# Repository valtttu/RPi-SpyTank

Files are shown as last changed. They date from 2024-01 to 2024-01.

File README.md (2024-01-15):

# RC-SpyTank project

> Valtteri Turkki

This repo contains documentation for Raspberry Pi SpyTank project. The idea was to make a fairly low-cost RC tracked vechile. The end result (in the current state) is shown in the below photo:

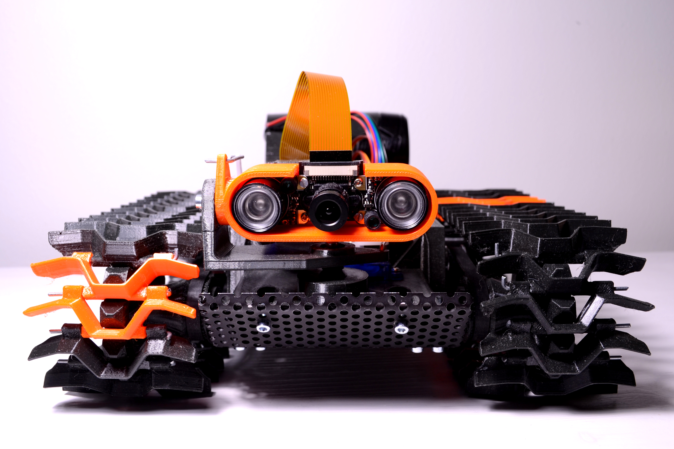
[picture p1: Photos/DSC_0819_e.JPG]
SpyTank


## Initial idea

Inspired by _RCTESTFLIGHT_ YouTube channels "_Tracked vehicles_" [playlist](https://youtube.com/playlist?list=PLXvxJNOIXBsN97d3_b5AXquRSAQOs3tVV&si=yVQvDruLYLw2IaSi), the idea was to build a RC-track vehicle for mainly indoor use. The key parameters are:

- Footprint of rougly one A4 sheet
- 3D printed tracks that can handle various types of terrain
- Controlling via Raspberry Pi
- Possibility to stream onboard night vision camera footage to phone
- Controlling with a bluetooth gamepad 
- Silent enough operation -> allows for spying in the dark

The 3D models for the tracks and pulleys that were used as the basis of the design are from _RCTESTFLIGHT_ Thingiverse page "_Snow Tank_" [https://www.thingiverse.com/thing:4308626](https://www.thingiverse.com/thing:4308626). Below photo shows that Snow Tank.

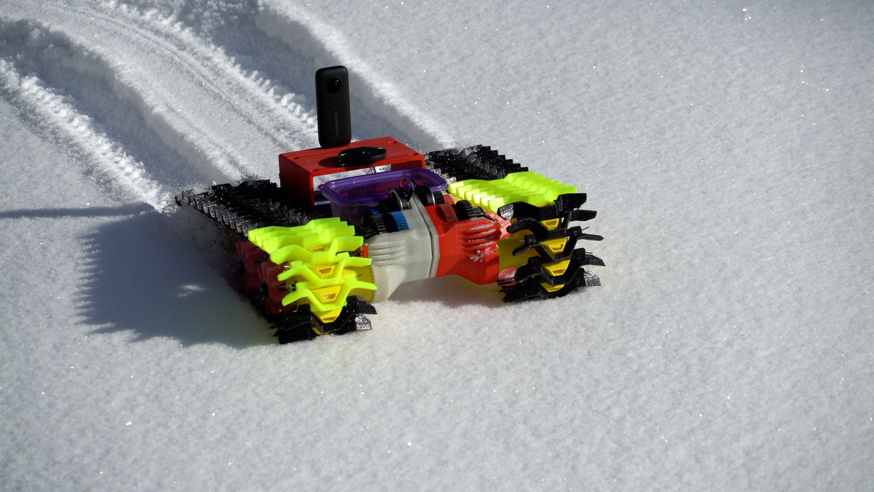
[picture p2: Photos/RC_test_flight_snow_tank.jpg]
Snow Tank by RCTESTFLIGHT


## Components

### Component choices explained

The main board was chosen to be Raspberry Pi zero 2 W as it has small footprint and power consumption, but it still allows you to plug-in the camera directly. The camera was chosen to be the ZeroCam night vision model as it plugs directly into the Pi Zero and allows decent image quality.

The motors were chosen to be NEMA 17 steppers due to the fact that they offer good torque and can be very silent with the Trinamic TMC2209 drivers. Also, as the tank was meant for silent operation and spying, the low top speed wasn't an issue. Furthermore, the NEMA 17 + TMC2209 combo costs as much as one good BLDC motor and you'd still need second motor and the controller...

The drilling machine battery was chosen as power supply as it's quite cheap and has a sturdy casing. If you have a 3S LiPo battery laying around, that's also a good option. The power conversion from 12v to 5v was made with a 'ghetto' solution: Buy a car USB adapter, tear it down and remove the connectors and there you have a step-down converter with 4 euros (compared to the fact that some step-down modules that can do >2A cost more than 20 euros).

### Component list

- Raspberry Pi Zero 2 W, link: [https://www.partco.fi/en/raspberry-pi/raspberry-pi-zero/23529-rpi-zero-2w.html](https://www.partco.fi/en/raspberry-pi/raspberry-pi-zero/23529-rpi-zero-2w.html)
- Night vision camera link: [https://raspberrypi.dk/en/product/zerocam-nightvision/](https://raspberrypi.dk/en/product/zerocam-nightvision/)
- Wireless retro gamepad controller 8BitDo, link: [Verkkokauppa.com](https://www.verkkokauppa.com/fi/product/625627/8BitDo-SN30-Pro-G-Classic-peliohjain-Switch-PC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)
- 2x NEMA 17 Stepper motor, link: [https://kauppa.sintosen.com/product/1266/nema-17-stepperi-moottori-18-astetta](https://kauppa.sintosen.com/product/1266/nema-17-stepperi-moottori-18-astetta)
- 2x TMC2209 v2.0 Stepper driver, link: [https://kauppa.sintosen.com/product/676/tmc2209-v20-stepperi-ohjain](https://kauppa.sintosen.com/product/676/tmc2209-v20-stepperi-ohjain) 
- 2x Miniature servo motor for camera tilting and panning (Tower pro 9g), link: [https://www.partco.fi/en/electromechanics/motors/servo-motors/20291-servo-sg90.html](https://www.partco.fi/en/electromechanics/motors/servo-motors/20291-servo-sg90.html)
- 2x OD: 13 mm, ID: 6 mm, width: 6 mm bearings for camera axes (recycled from bicycle pedals), link: [https://www.ebay.co.uk/itm/266305894814](https://www.ebay.co.uk/itm/266305894814)
- 2x Timing belt 160 mm, link: [https://kauppa.sintosen.com/product/899/hammashihna-gt2-6mm-160mm-lenkki](https://kauppa.sintosen.com/product/899/hammashihna-gt2-6mm-160mm-lenkki)
- 2x Pulley, link: [https://kauppa.sintosen.com/product/582/ajoituspyora-gt2-20-hammasta-6mm-hihnalle](https://kauppa.sintosen.com/product/582/ajoituspyora-gt2-20-hammasta-6mm-hihnalle)
- Drilling machince battery Tamforce+ 12v 2Ah, link: [https://www.puuilo.fi/tamforce-akku-12v-2ah](https://www.puuilo.fi/tamforce-akku-12v-2ah)
- 12v to 5v step-down converter for Pi and servos, link: [https://www.puuilo.fi/axxel-usb-autolaturi-12v-kahdella-portilla](https://www.puuilo.fi/axxel-usb-autolaturi-12v-kahdella-portilla)
- 8x 6mm bearings for the wheels, link: [https://hobbyfactory.fi/p41450/avid-6x12x4-revolution-1kpl](https://hobbyfactory.fi/p41450/avid-6x12x4-revolution-1kpl)
- 2x springs for track tensioning, link: [https://hobbyfactory.fi/p41913/team-associated-91834-front-shock-springs-yellow-4-30-lb-in-l44mm](https://hobbyfactory.fi/p41913/team-associated-91834-front-shock-springs-yellow-4-30-lb-in-l44mm)
- 2x M5 bolt with 75 mm length for the track tensoner shaft
- 2x 6 mm rod, length 108 mm for the electronics rail
- 78 mm x 66 mm PCB for soldering the electronics
- M6 threaded rod for axles, link: [https://www.puuilo.fi/kierretanko-rst-a2-1m-m6](https://www.puuilo.fi/kierretanko-rst-a2-1m-m6)
- 1 mm sheet metal with 3 mm holes for the base plate
- approx. 50x M3 nuts and bolts (from 10 mm to 20 mm in length)

## Mechanical solutions

Here are explained some of the key mechanical features of the SpyTank:

### 1) Component placing



The use of perforated steel sheet with 3 mm holes as base plate allows to mount things easily and flexibly. All of the bolts to the bottom are M3 and the 3D models have slotted holes for the bolts, so that the exact position of the parts can be adjusted. The distribution of components is made so that the center of mass of the tank is quite well in the center and thus the tracks should have the lowest possible pressure.

### 2) Camera pan and tilt system

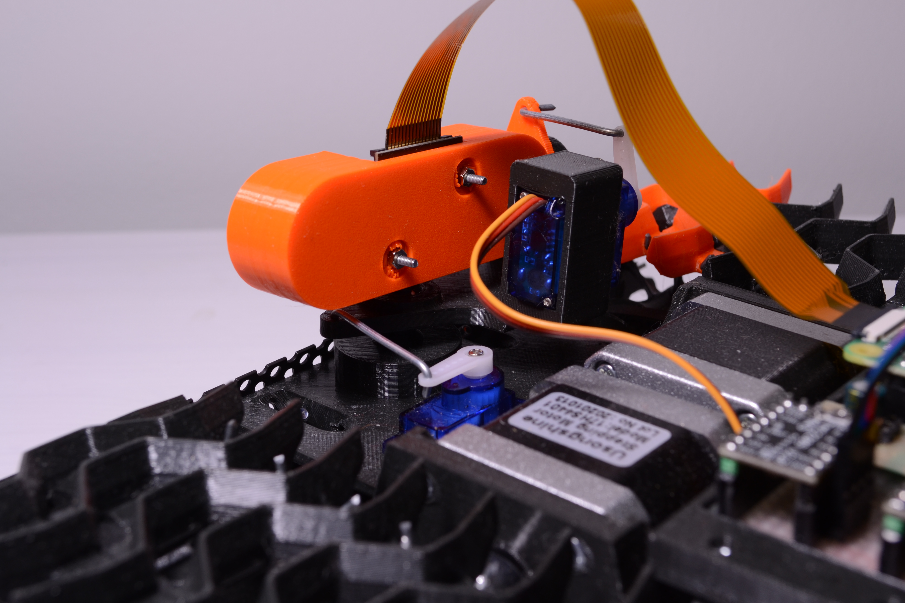
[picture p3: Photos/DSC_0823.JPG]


The pan & tilt functionality for the camera is done with 2 miniature servos and liknages made from the same steel wire as the track pins. The axes have bearings to enable smooth rotation. The holes in the servo arms had to be enlargened for the steel wire.

### 3) Front axis and belt tensioning



As the tank has tracks and belt drive, it means that the wheelbase and drive axle to motor shaft distances have to be modifiable. This is done so that motors are fixed on their place, but the front axle has slots in the track direction and thus the belt tension is adjusted by moving the front axle forward or backward. The gear ration is 2:1 which gives the tank already enough torque to climb a hill so steep that it will land on its roof.

### 4) Track tensioning and electronics mounting



In order to allow the track to adapt to the terrain, the rear axle is spring loaded with the tensioning system in the photo above. The axle goes through a holder that has M5 nut intergrated to it. The holder is then installed to a slider mount that also has the RC vehicle spring to provide the tension. To keep things moving linearly, a M5 bolt (75 mm) with the head cut away and a notch made for tightening is inserted to the center.

The electronics PCB and the battery are mounted on two rails. This allows easy attachement of them and also leaves room for future modifiability, in case the electronics gets updated.

## Programming and circuits

### The basic idea of interfaces

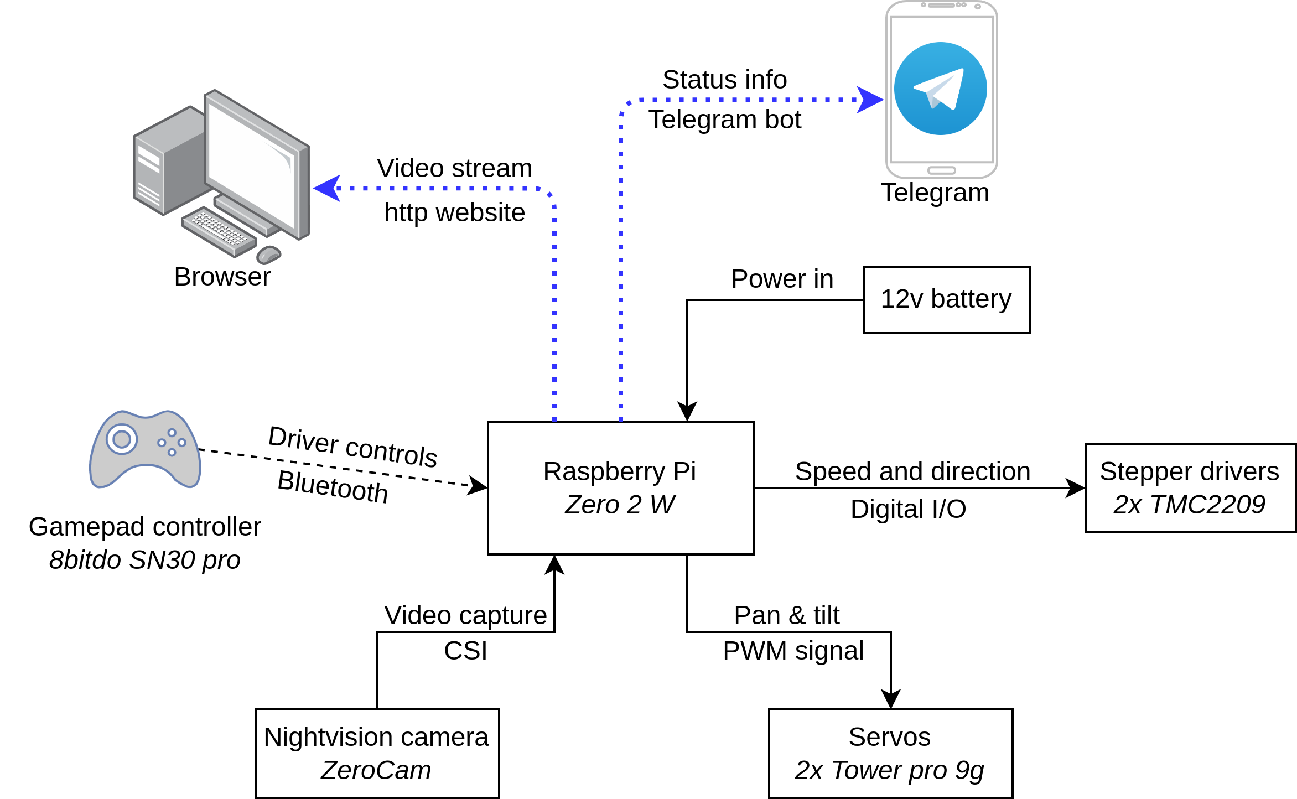
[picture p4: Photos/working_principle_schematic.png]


The 'mechatronic design schematic' of the SpyTank is shown in the above figure. 

### Wiring schematic

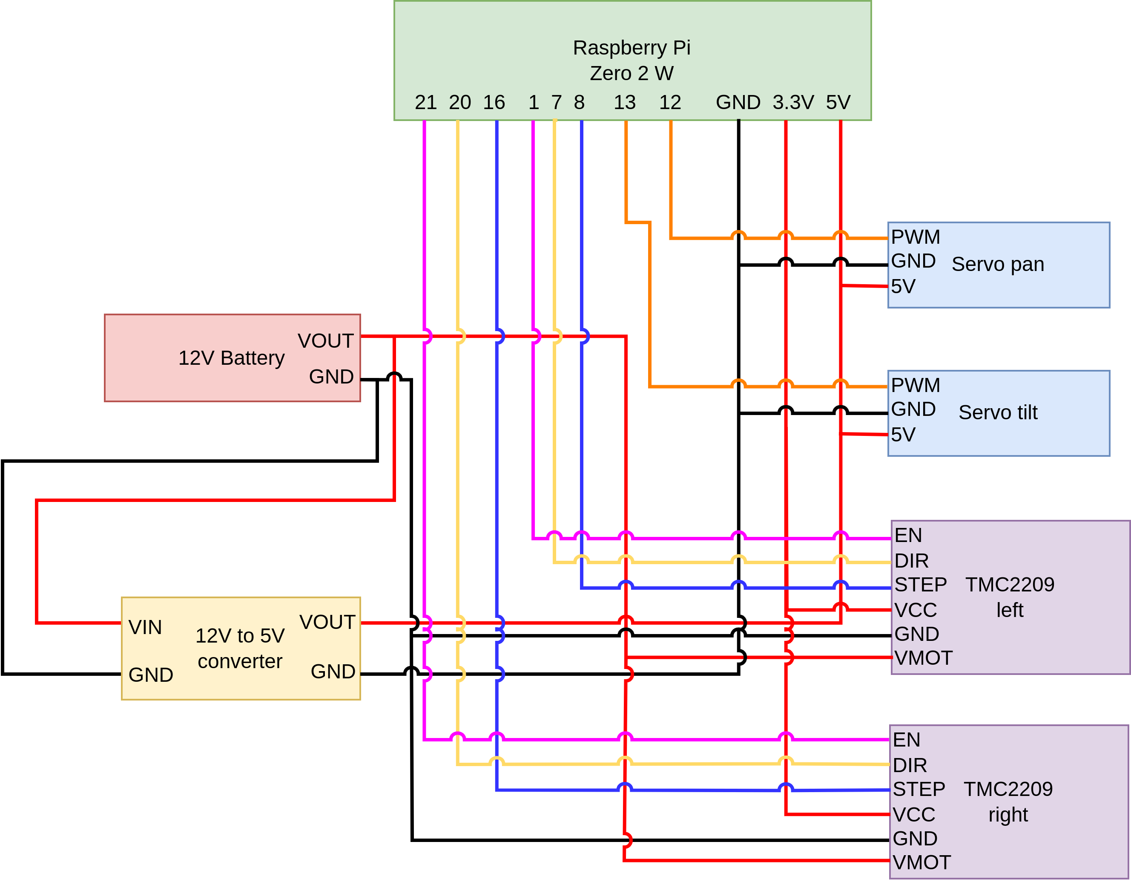
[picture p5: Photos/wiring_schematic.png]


The circuit plan pf the tank is shown above.

### Programming part

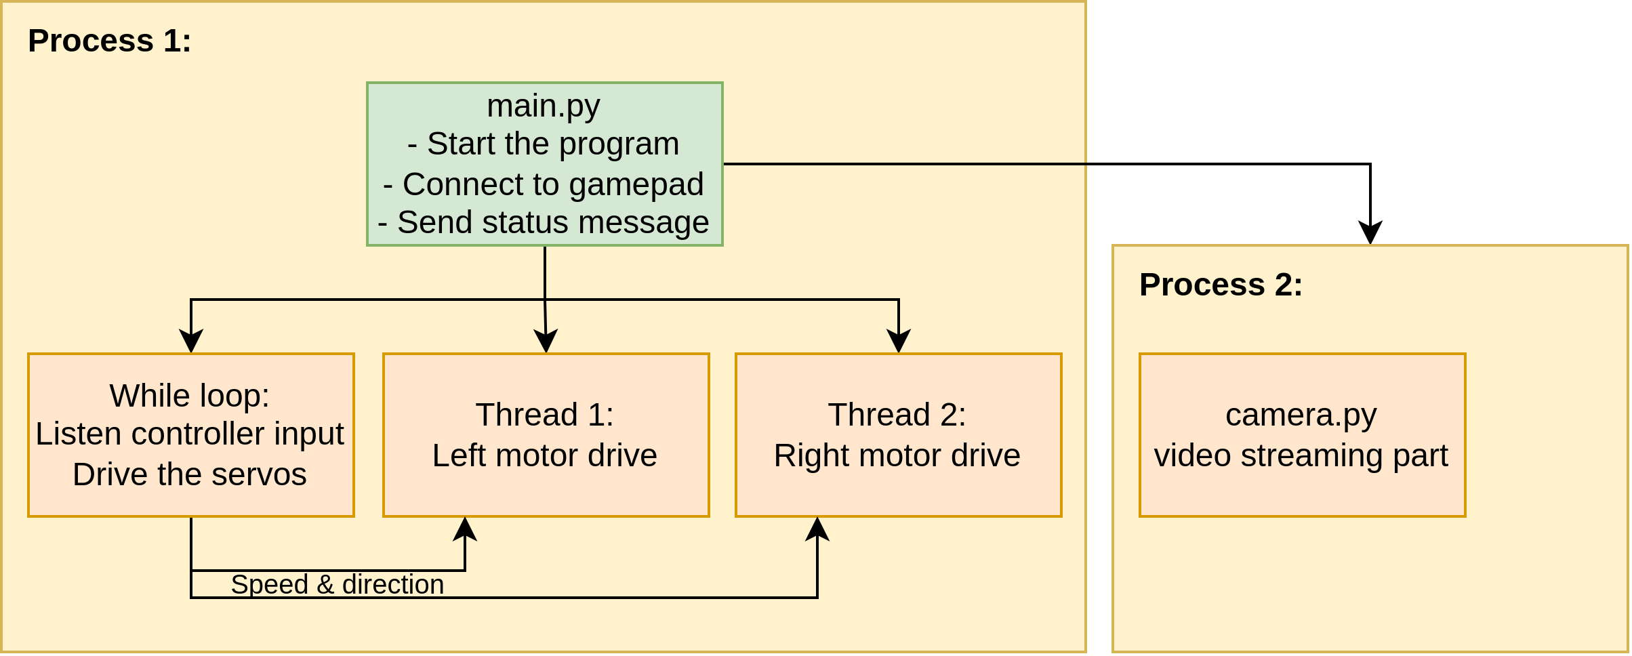
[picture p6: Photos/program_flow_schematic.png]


The diagram above explains the program logic of the SpyTank. There are 3 classes: `camera`, `motors` (in `stepper.py`) and `controller`. 

The camera class controls the servos of the camera stage and starts the stream. The stream works independently in its own process and is in the `server.py` script. The script is direcly the one from [github.com/waveform80/pistreaming/](https://github.com/waveform80/pistreaming/) with slight modifications to the paths, so that the script can be run from any directory. 

The motors class takes care of converting the input from the controller analog axis [-1, 1] to direction and step delay for right and left motor. Thus, the control is tank-like, ie. you use left analog stick to control left track and the right one for right track. The conversion for the delay is done linearly and there'a a cut-off so that input smaller than it maps to zero velocity $\rightarrow$ motors off.

The controller class takes care of mapping the buttons and axes of the gamepad controller to input. As `pyglet` didn't seem to work with the SN30 Pro controller in wireless more, the controller mapping is done with `evdev`. The implementation is such that adding new buttons should be rather straight forward (the mappings are told in `main.py`). To find more info how to use `evdev` and where the numbers come from, see [python-evdev.readthedocs.io/en/latest/](https://python-evdev.readthedocs.io/en/latest/).

The script `utils.py` contains some accessory functions that make the `main.py` cleaner to read. The Telegram bot messaging is made so that the bot credentials are stored in file `secrets.dat` in format `secret-name;secret-value` and read from there using function `read_credentials()`. Then the code finds the IP local address of the PI and parses a message that contains the IP and the stream link. The message is sent using the bot API as follows
```
url = f"https://api.telegram.org/bot{data['TOKEN']}/sendMessage?chat_id={data['ID']}&text={message}"
    requests.get(url).json()
```
where `TOKEN` is the bot token and `ID` is your Telegram ID (can be found by googling _"How to find my Telegram ID"_ and asking it from a bot).

Finally, to make the `main.py` run on boot up, the `rc.local` file of the Pi has to be modified accordingly: Add lines

```
sleep 15
sudo python3 /home/user-name/SpyTank/Code/main.py &
```
above the `exit 0`. Modify the path to match your code location and note the `&` as otherwise the code will stop the boot (`rc.local` will never exit). This will give the PI time to find network connection etc. After this, the `controller.connect()` method has a default timeout of 40 seconds. If the connection to that gamepad controller is not estabilised in this time, the code will exit.

## Additional instructions

### Baseplate cutting and bending

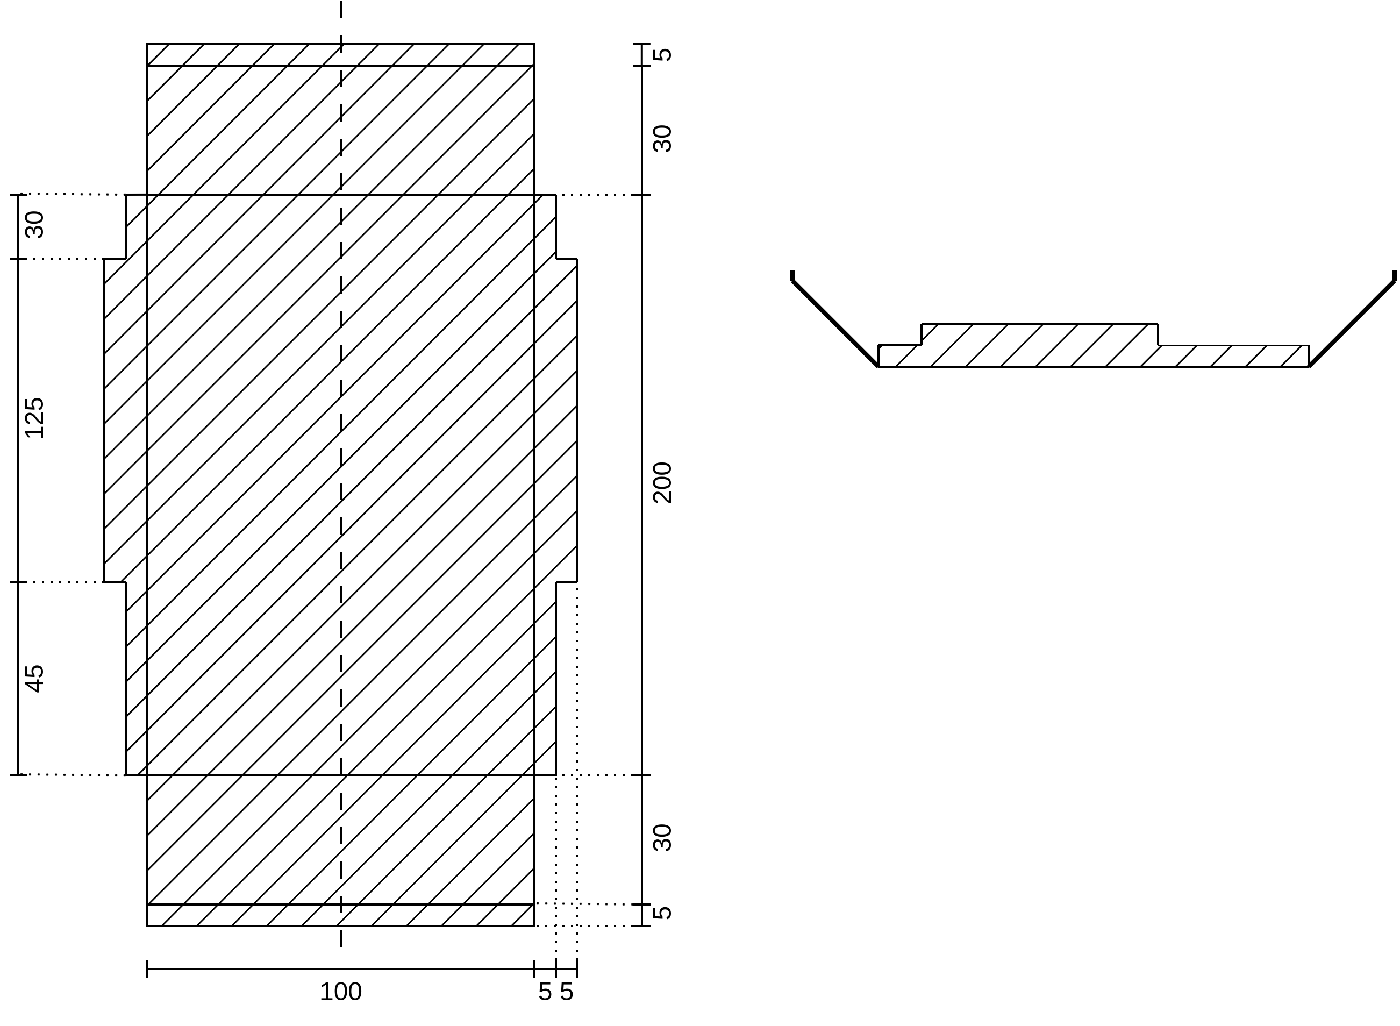
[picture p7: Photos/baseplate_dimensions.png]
Baseplate dimensions


Above is shown the baseplate dimensions. The plate is bent so that the ends are at 45 degree angle with respect to the bottom and the final parts are vertical. The sides are at 90 degree angle w.r.t. the bottom part.

### 3D printing specs

| **Model name** | **Orientation** | **Supports** | **Print in places**|
|---|---|---|---|
| `camera_base.stl` | As installed (pan axis along z-axis) | From the build plate | Insert 1x M3 nut | 
| `camera_holder.stl` | Backside (with the 2 holes) facing down | From the build plate | Insert 1x M3 nut | 
| `camera_pan_stage.stl` | As installed (pan axis along z-axis) | From the build plate | None | 
| `front_axle_holder.stl` | Axle hole aligned with z-axis | None | None |
| `front_axle_spacer.stl` | Hole aligned with z-axis | None | None |
| `front_pulley.stl` | The outside face of the pulley to build plate | None | None |
| `nema17_mount.stl` | Largest flat face to build plate | None | None |
| `rear_axle_holder.stl` | Axle hole aligned with horizontally | None | Insert 1x M5 nut |
| `rear_axle_holder_slider.stl` | So that the slotted hole on on the top is horizontally | None | None |
| `rear_axle_spacer.stl` | Axle hole aligned with z-axis | None | None |
| `rear_pulley.stl` | Same as `front_pulley.stl`| None | None |
| `track_link.stl` | So that the track pin holes are horizontally | None | None |
| `drill_battery_holder.stl` | The flat face with 2 holes facing down | Use enforcers for the rail mounts | None |
| `pcb_carrier.stl` | Top part (largest flat face) facing down | None | Insert the main PCB and 6x M3 nuts for enclosure attachment |
| `rail_holder_back.stl` | Rail hole axis aligned with the z-axis, holes opening upwards | None | None |
| `rail_holder_front.stl` | Axle hole aligned with z-axis, holes opening upwards | None | None |
| `rpi_pcb_spacer.stl` | Axle aligned with z-axis| None | None |
| `stepper_wire_connector.stl` | PCB and slotted holes vertically | None | Insert a small PCB |

All parts were printed with Prusa Mini using 0.4 mm nozzle and PETG filament. The default layer height was 0.25 mm (draft quality) and variable layer height was used for parts with holes that have to be precise and have axis perpendicular to z-axis while printing. For high mechanical stress parts (axle holders and pulleys), the number of perimeters was increased to 3 from the default 2.

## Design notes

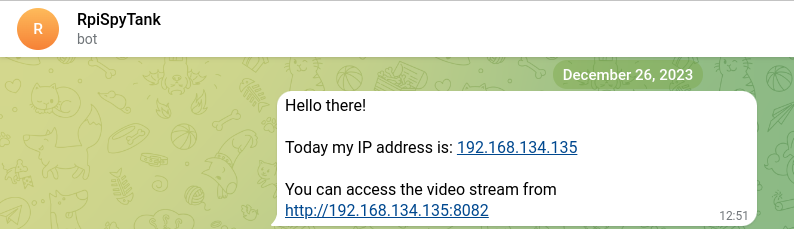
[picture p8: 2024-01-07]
Photos/telegram_bot_message.png

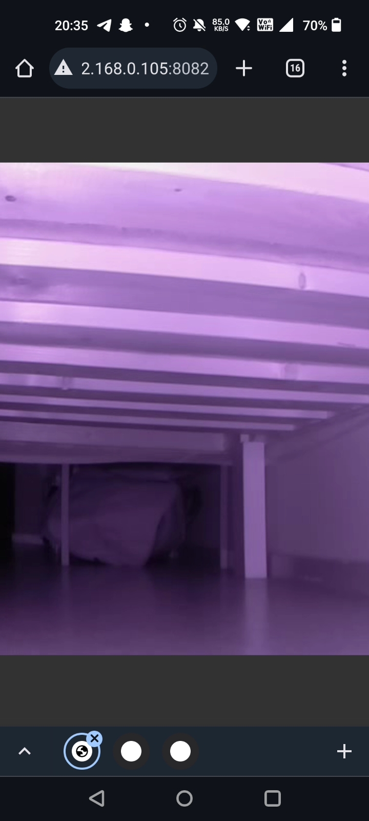
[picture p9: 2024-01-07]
Photos/nightvision_stream.jpg

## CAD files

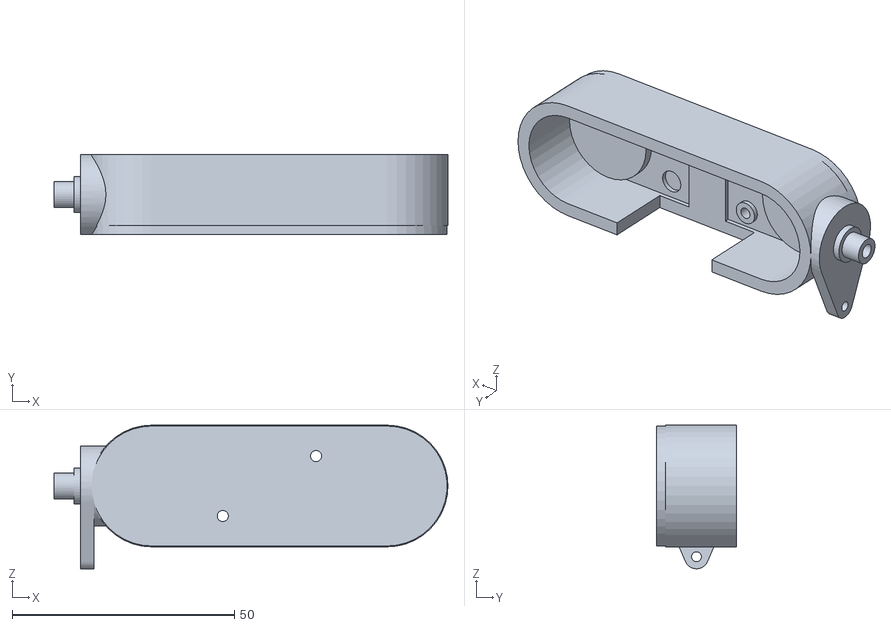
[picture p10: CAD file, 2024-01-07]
Models/Camera/camera_holder.STL
88.7 x 18.0 x 32.3

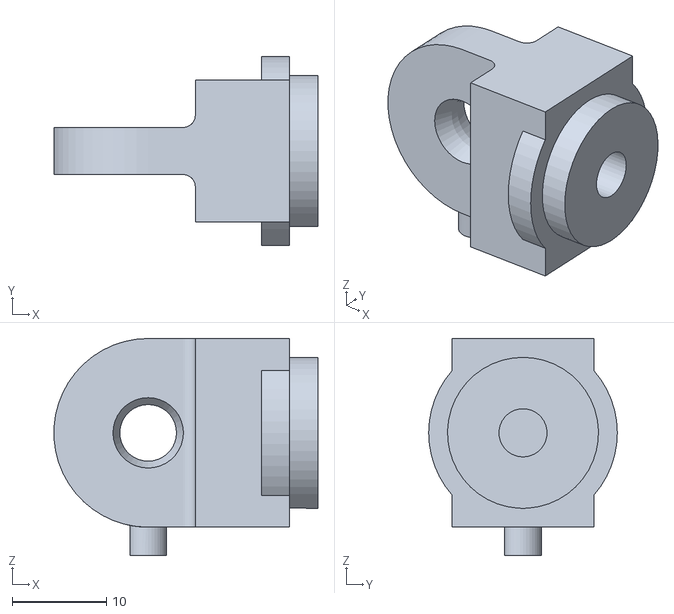
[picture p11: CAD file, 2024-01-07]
Models/Drivetrain/rear_axle_holder.STL
28.0 x 20.0 x 23.0

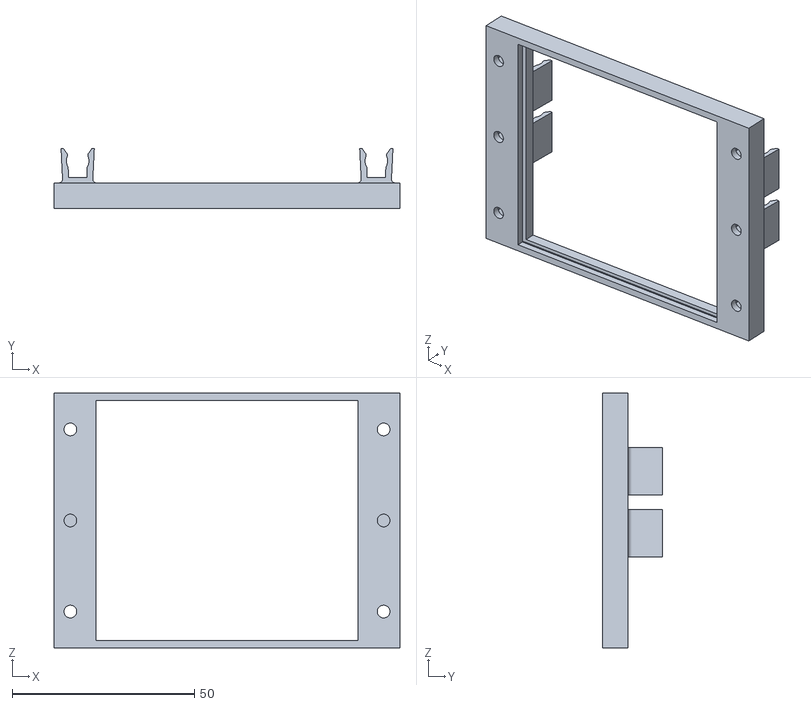
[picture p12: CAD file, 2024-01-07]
Models/Electronics/pcb_carrier.STL
95.0 x 16.4 x 70.0

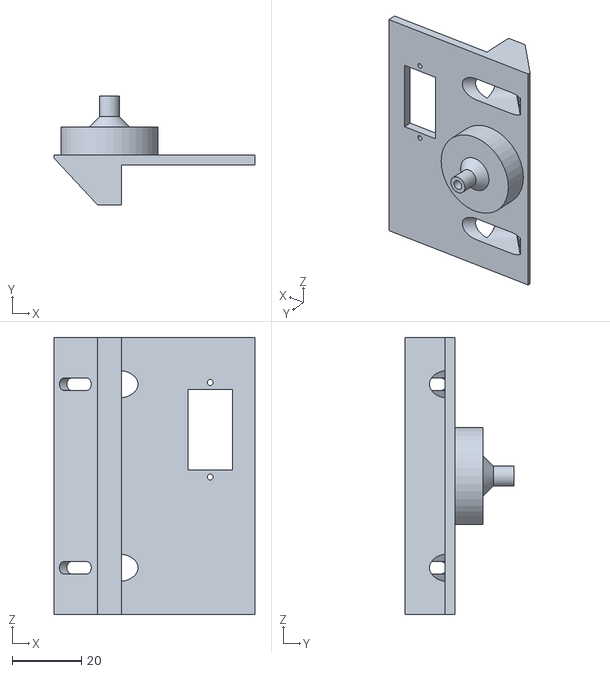
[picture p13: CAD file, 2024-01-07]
Models/Camera/camera_base.STL
58.0 x 31.5 x 80.0

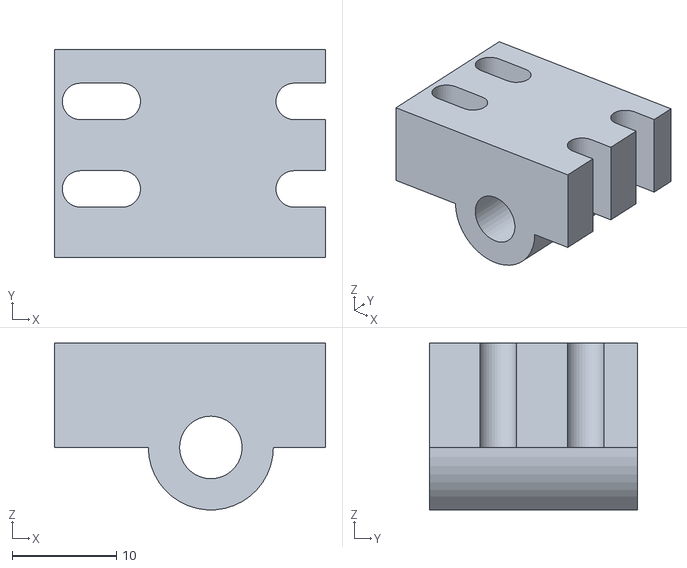
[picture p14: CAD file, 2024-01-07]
Models/Drivetrain/front_axle_holder.STL
26.0 x 20.0 x 16.0

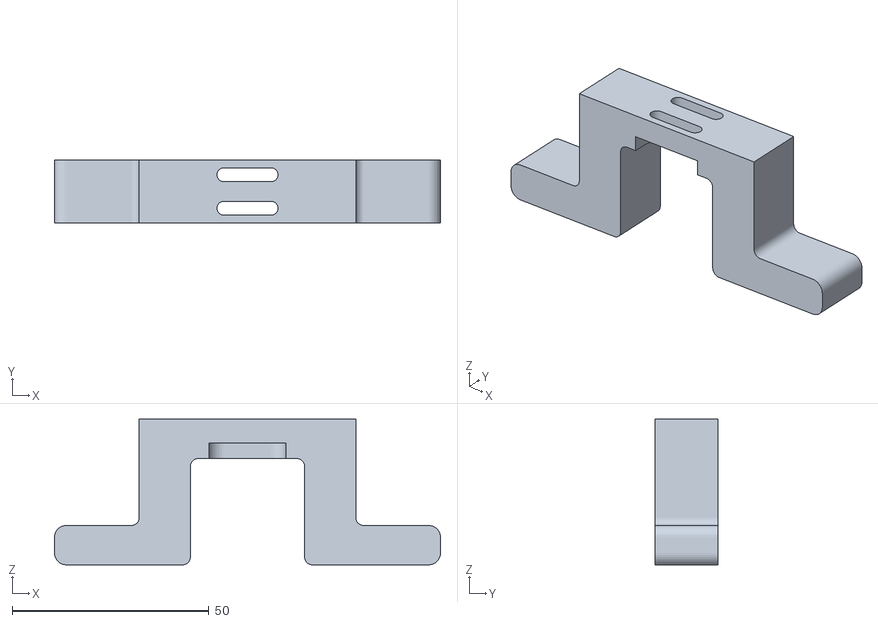
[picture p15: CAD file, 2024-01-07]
Models/Electronics/rail_holder_front.STL
98.0 x 16.0 x 37.0

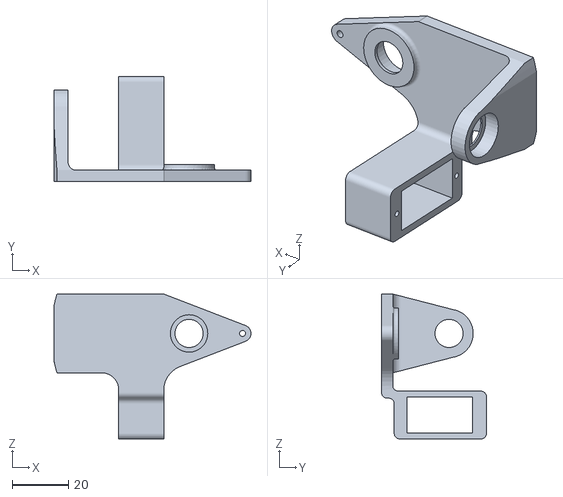
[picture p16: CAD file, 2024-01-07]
Models/Camera/camera_pan_stage.STL
70.0 x 37.3 x 51.5

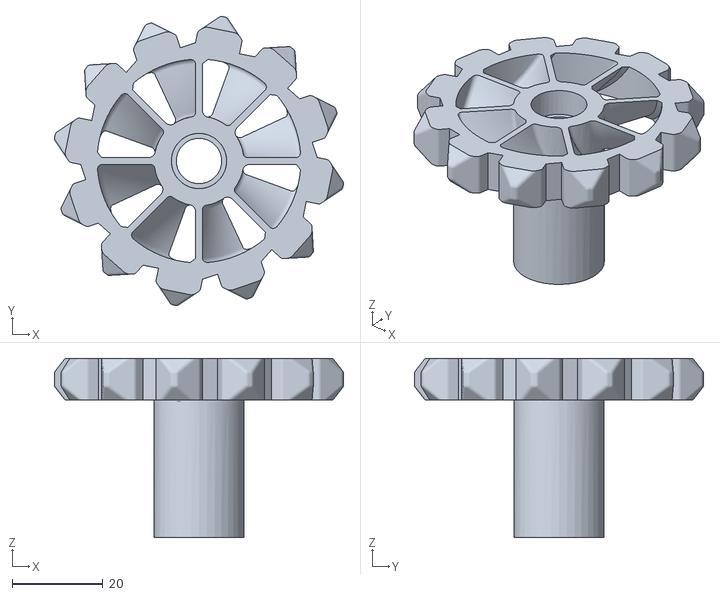
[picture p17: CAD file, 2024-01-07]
Models/Drivetrain/rear_pulley.STL
63.8 x 63.8 x 39.6

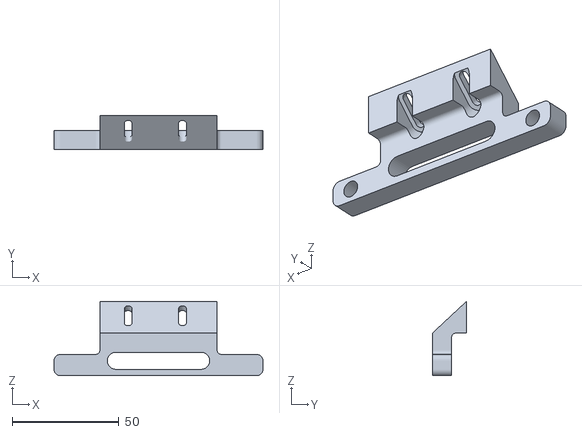
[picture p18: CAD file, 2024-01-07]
Models/Electronics/rail_holder_back.STL
98.0 x 16.0 x 34.9

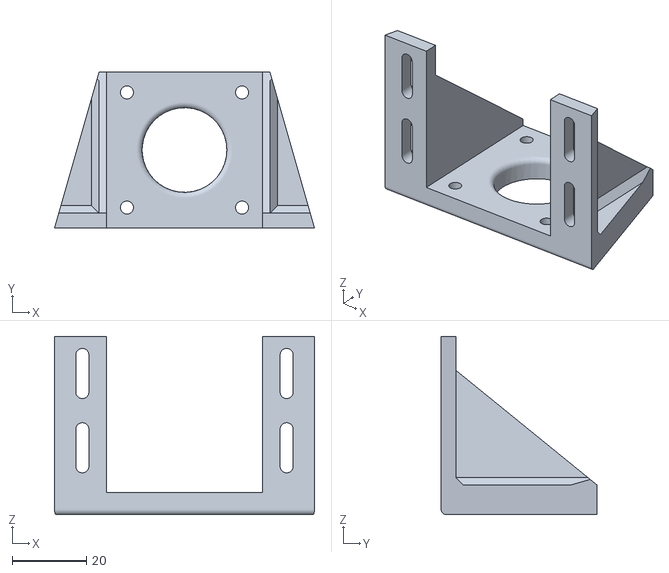
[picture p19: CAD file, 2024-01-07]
Models/Drivetrain/nema17_mount.STL
70.0 x 42.0 x 48.0

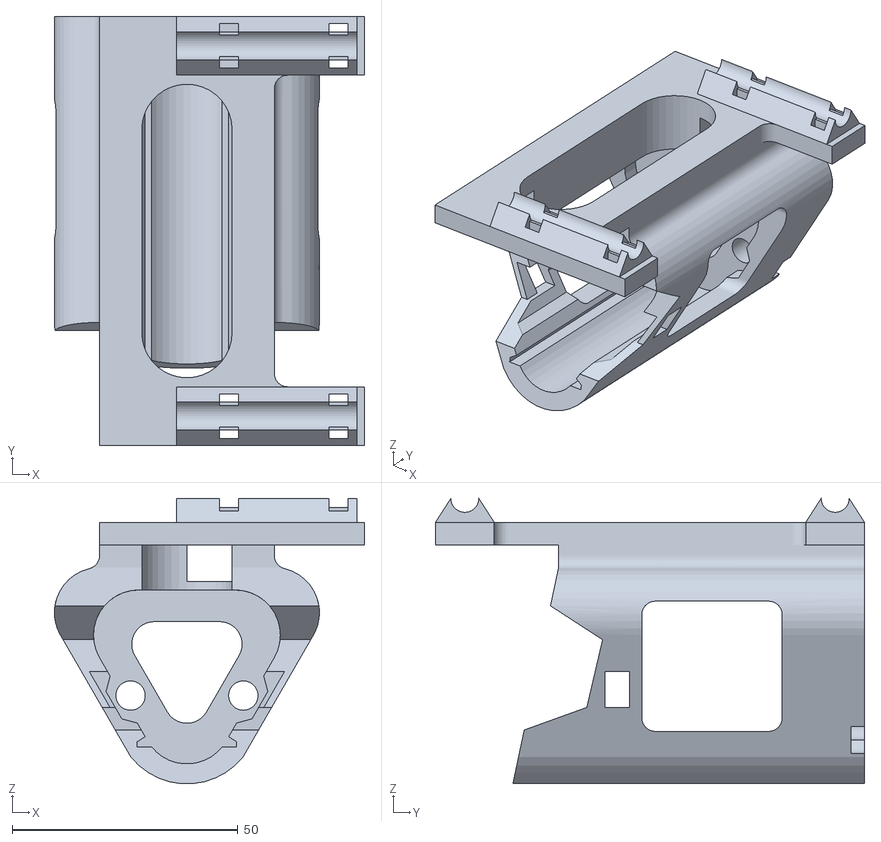
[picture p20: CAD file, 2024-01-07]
Models/Electronics/drill_battery_holder.STL
68.7 x 95.0 x 63.2

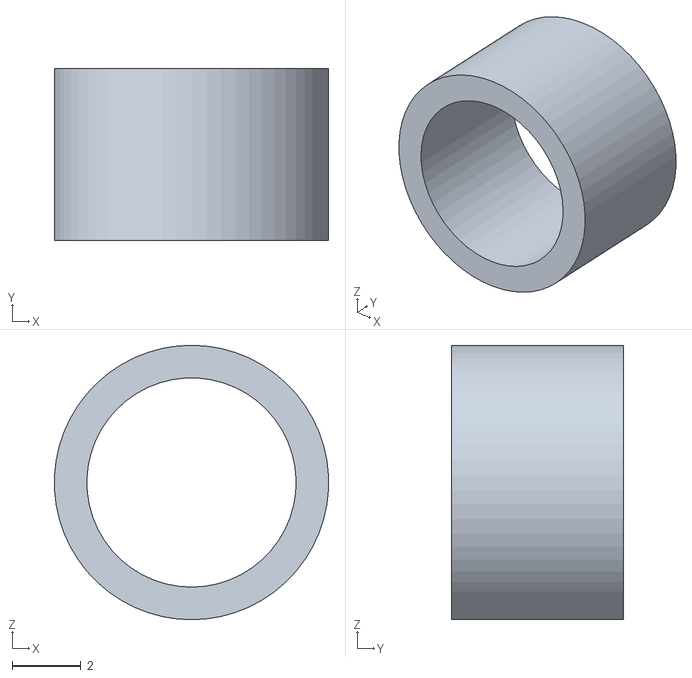
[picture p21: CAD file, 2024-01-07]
Models/Drivetrain/front_axle_spacer.STL
7.99 x 5.00 x 8.00

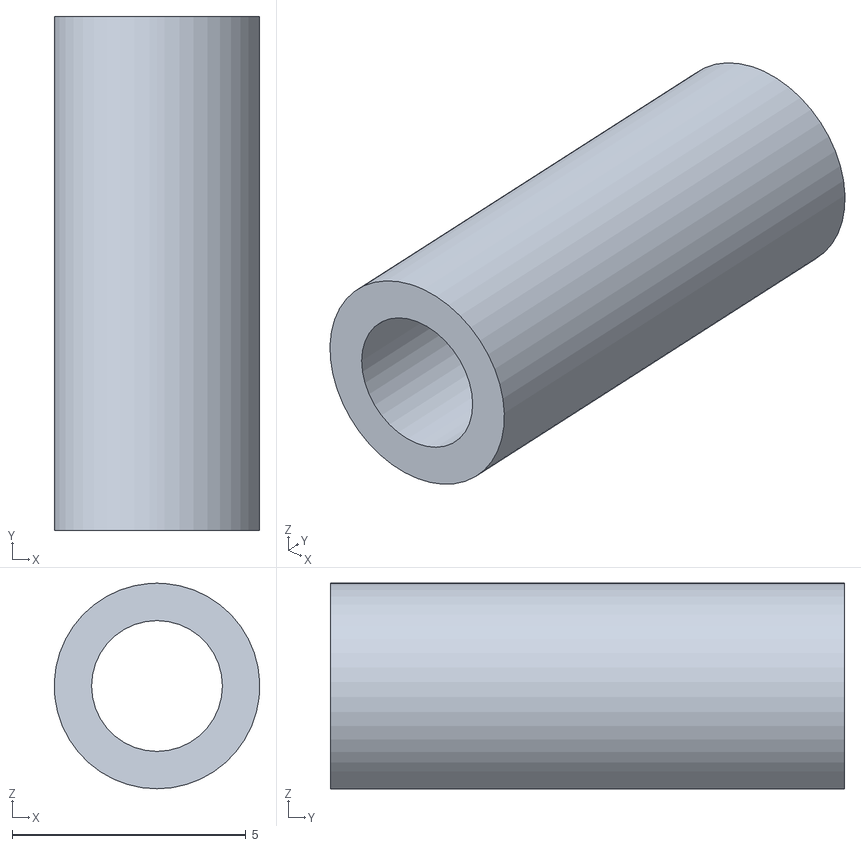
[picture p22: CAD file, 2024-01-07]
Models/Electronics/rpi_pcb_spacer.STL
4.40 x 11.0 x 4.40

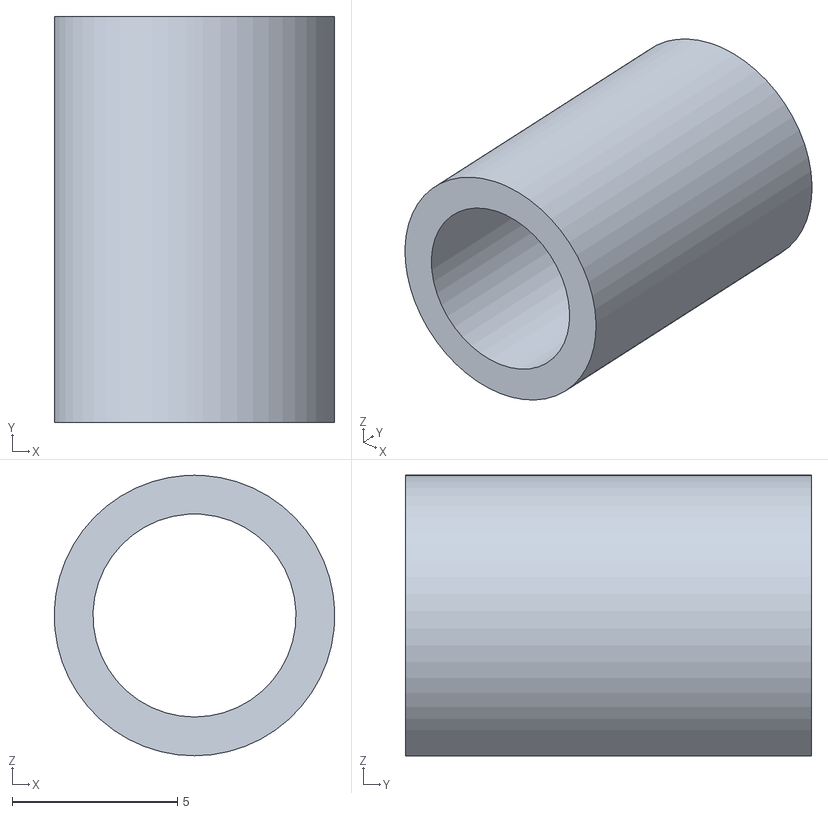
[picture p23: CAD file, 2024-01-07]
Models/Drivetrain/rear_axle_spacer.STL
8.50 x 12.3 x 8.50

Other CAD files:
Models/Electronics/stepper_wire_connector.STL
Models/Drivetrain/rear_axle_holder_slider.STL
Models/Drivetrain/track_link.STL
Models/Drivetrain/front_pulley.STL

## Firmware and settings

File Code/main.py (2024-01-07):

import controller
import stepper
import camera
import utils
import time

axes = {'RX': 3,
        'RY': 4,
        'LX': 0,
        'LY': 1}

dpad = {'DPX': 16,
        'DPY': 17}

buttons = {'RS': 309, 'LS': 308, 'SEL': 310, 'A': 305}

en = [21, 1]
step = [16, 8]
dir = [20, 7]


gp = controller.gamepad()
gp.connect('8bitdo', axes, dpad, buttons)

mot = stepper.motors(en, dir, step)
cam = camera.camera(12,13)

mot.activate()
mot.map_velocity([0, 0])

if(utils.has_internet()):
    utils.announce_ip()
    cam.start_stream()

while gp.check_connection():
    vels = gp.read_axes(['LY', 'RY'])
    mot.set_enable(gp.read_buttons(['LS', 'RS']))
    mot.map_velocity(vels)
    
    utils.map_dpad(gp.read_dpad(), cam)
    
    if(gp.read_buttons(['A'])[0]):
        cam.home()

    if(gp.read_buttons(['SEL'])[0]):
        break
    
mot.deactivate()
cam.stop_stream()

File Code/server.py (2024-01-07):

#!/usr/bin/env python

# This code is fully from https://github.com/waveform80/pistreaming/ except 
# for the added full paths that make it possible to run the code from anywhere

import sys
import io
import os
import shutil
from subprocess import Popen, PIPE
from string import Template
from struct import Struct
from threading import Thread
from time import sleep, time
from http.server import HTTPServer, BaseHTTPRequestHandler
from wsgiref.simple_server import make_server

import picamera
from ws4py.websocket import WebSocket
from ws4py.server.wsgirefserver import (
    WSGIServer,
    WebSocketWSGIHandler,
    WebSocketWSGIRequestHandler,
)
from ws4py.server.wsgiutils import WebSocketWSGIApplication

###########################################
# CONFIGURATION
WIDTH = 640
HEIGHT = 480
FRAMERATE = 24
HTTP_PORT = 8082
WS_PORT = 8084
COLOR = u'#444'
BGCOLOR = u'#333'
JSMPEG_MAGIC = b'jsmp'
JSMPEG_HEADER = Struct('>4sHH')
VFLIP = True
HFLIP = True

###########################################


class StreamingHttpHandler(BaseHTTPRequestHandler):
    def do_HEAD(self):
        self.do_GET()

    def do_GET(self):
        if self.path == '/':
            self.send_response(301)
            self.send_header('Location', '/index.html')
            self.end_headers()
            return
        elif self.path == '/jsmpg.js':
            content_type = 'application/javascript'
            content = self.server.jsmpg_content
        elif self.path == '/index.html':
            content_type = 'text/html; charset=utf-8'
            tpl = Template(self.server.index_template)
            content = tpl.safe_substitute(dict(
                WS_PORT=WS_PORT, WIDTH=WIDTH, HEIGHT=HEIGHT, COLOR=COLOR,
                BGCOLOR=BGCOLOR))
        else:
            self.send_error(404, 'File not found')
            return
        content = content.encode('utf-8')
        self.send_response(200)
        self.send_header('Content-Type', content_type)
        self.send_header('Content-Length', len(content))
        self.send_header('Last-Modified', self.date_time_string(time()))
        self.end_headers()
        if self.command == 'GET':
            self.wfile.write(content)


class StreamingHttpServer(HTTPServer):
    def __init__(self):
        super(StreamingHttpServer, self).__init__(
                ('', HTTP_PORT), StreamingHttpHandler)
        with io.open(os.path.dirname(__file__) +  '/index.html', 'r') as f:
            self.index_template = f.read()
        with io.open(os.path.dirname(__file__) +  '/jsmpg.js', 'r') as f:
            self.jsmpg_content = f.read()


class StreamingWebSocket(WebSocket):
    def opened(self):
        self.send(JSMPEG_HEADER.pack(JSMPEG_MAGIC, WIDTH, HEIGHT), binary=True)


class BroadcastOutput(object):
    def __init__(self, camera):
        print('Spawning background conversion process')
        self.converter = Popen([
            'ffmpeg',
            '-f', 'rawvideo',
            '-pix_fmt', 'yuv420p',
            '-s', '%dx%d' % camera.resolution,
            '-r', str(float(camera.framerate)),
            '-i', '-',
            '-f', 'mpeg1video',
            '-b', '800k',
            '-r', str(float(camera.framerate)),
            '-'],
            stdin=PIPE, stdout=PIPE, stderr=io.open(os.devnull, 'wb'),
            shell=False, close_fds=True)

    def write(self, b):
        self.converter.stdin.write(b)

    def flush(self):
        print('Waiting for background conversion process to exit')
        self.converter.stdin.close()
        self.converter.wait()


class BroadcastThread(Thread):
    def __init__(self, converter, websocket_server):
        super(BroadcastThread, self).__init__()
        self.converter = converter
        self.websocket_server = websocket_server

    def run(self):
        try:
            while True:
                buf = self.converter.stdout.read1(32768)
                if buf:
                    self.websocket_server.manager.broadcast(buf, binary=True)
                elif self.converter.poll() is not None:
                    break
        finally:
            self.converter.stdout.close()


def main():
    print('Initializing camera')
    with picamera.PiCamera() as camera:
        camera.resolution = (WIDTH, HEIGHT)
        camera.framerate = FRAMERATE
        camera.vflip = VFLIP # flips image rightside up, as needed
        camera.hflip = HFLIP # flips image left-right, as needed
        sleep(1) # camera warm-up time
        print('Initializing websockets server on port %d' % WS_PORT)
        WebSocketWSGIHandler.http_version = '1.1'
        websocket_server = make_server(
            '', WS_PORT,
            server_class=WSGIServer,
            handler_class=WebSocketWSGIRequestHandler,
            app=WebSocketWSGIApplication(handler_cls=StreamingWebSocket))
        websocket_server.initialize_websockets_manager()
        websocket_thread = Thread(target=websocket_server.serve_forever)
        print('Initializing HTTP server on port %d' % HTTP_PORT)
        http_server = StreamingHttpServer()
        http_thread = Thread(target=http_server.serve_forever)
        print('Initializing broadcast thread')
        output = BroadcastOutput(camera)
        broadcast_thread = BroadcastThread(output.converter, websocket_server)
        print('Starting recording')
        camera.start_recording(output, 'yuv')
        try:
            print('Starting websockets thread')
            websocket_thread.start()
            print('Starting HTTP server thread')
            http_thread.start()
            print('Starting broadcast thread')
            broadcast_thread.start()
            while True:
                camera.wait_recording(1)
        except KeyboardInterrupt:
            pass
        finally:
            print('Stopping recording')
            camera.stop_recording()
            print('Waiting for broadcast thread to finish')
            broadcast_thread.join()
            print('Shutting down HTTP server')
            http_server.shutdown()
            print('Shutting down websockets server')
            websocket_server.shutdown()
            print('Waiting for HTTP server thread to finish')
            http_thread.join()
            print('Waiting for websockets thread to finish')
            websocket_thread.join()


if __name__ == '__main__':
    main()

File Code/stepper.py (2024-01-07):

# This file contains class for the drive stepper motors

import RPi.GPIO as GPIO
GPIO.setmode(GPIO.BCM)
#GPIO.setwarnings(False)
import time
import threading
from typing import List

n_motors = 2
dir = [True, False]
slack = 0.001
del_max = 0.001
del_min = 2e-6

# Class for two stepper motors
class motors:

    def __init__(self, en_pins: List[int], dir_pins: List[int], step_pins: List[int]):
        # Save the pins numbers
        self._en_pins = en_pins
        self._dir_pins = dir_pins
        self._step_pins = step_pins

        # Initialize GPIO
        for i in range(n_motors):
            GPIO.setup(self._step_pins[i], GPIO.OUT)
            GPIO.setup(self._dir_pins[i], GPIO.OUT)
            GPIO.setup(self._en_pins[i], GPIO.OUT)

        # Set initially to stop, delay to 1 sec and direction to 1 = forward
        self._run = [False, False]
        self._delay = [1, 1]
        self._direction = [1, 1]
        self._drive_thread = [1, 1]
        self._active = False

        # Enable the motors
        for i in range(n_motors):
            GPIO.output(self._en_pins[i], GPIO.LOW)


    def map_velocity(self, input: List[float]):
        '''
            Function for mapping velocity (including direction) from [-1, 1] to delay between step commands
        '''

        if(len(input) != n_motors):
            raise ValueError('Incorrect number of inputs in the list')

        for i in range(n_motors):
            if(abs(input[i]) > slack):
                # Determine direction
                if(input[i] < 0):
                    self._direction[i] = 0
                else:
                    self._direction[i] = 1

                # Determine delay
                self._run[i] = True
                self._delay[i] = (del_min-del_max)*abs(input[i]) + del_max # Map from [0,1] to [del_max, del_min]
            else:
                self._run[i] = False

    def set_enable(self, input: List[bool]):
        '''
            Function for setting the state of the enable pins --> Allows freewheeling
        '''

        if(len(input) != n_motors):
            raise ValueError('Incorrect number of inputs in the list')

        for i in range(n_motors):
            GPIO.output(self._en_pins[i], input[i])


    def activate(self):
        self._active = True
        for i in range(n_motors):
            self._drive_thread[i] = threading.Thread(target=self._run_motor, args=(i,))
            self._drive_thread[i].start()


    def deactivate(self):
        if(self._active):
            self._active = False
            for i in range(n_motors):
                self._drive_thread[i].join()
            GPIO.cleanup()



    def _run_motor(self, num: int):
        '''
            Function that gives the motor the drive signal, needs to be run in separate thread
        '''
                
        while(self._active):

            # Set direction
            GPIO.output(self._dir_pins[num], (dir[num] ^ self._direction[num]))

            # Give the step signal
            if(self._run[num]):
                GPIO.output(self._step_pins[num], GPIO.LOW)
                time.sleep(self._delay[num])
                GPIO.output(self._step_pins[num], GPIO.HIGH)
                time.sleep(self._delay[num])
            else:
                time.sleep(del_max)

                

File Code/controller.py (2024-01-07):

# This file contains class for the gamepad controller

import RPi.GPIO as GPIO
import evdev
import time
from typing import List, Dict


# Class for gamepad controller
class gamepad:

    def __init__(self):
        self._dev_path = ''
        self._is_connected = False


    def connect(self, name: str, abs_axes: Dict[str, int], dpad: Dict[str, int], buttons: Dict[str, int], wait = True, timeout = 40):
        '''
            Connect to controller (or device) with specific name and with specific axis mapping
            and button mapping
            If the device is not found after timeout an IOerror is raised
        '''
        t_start = time.time()
        found = False
        while(not found and time.time()-t_start < timeout):
            dev_list = evdev.list_devices()
            self._dev_path = ''
            for dev in dev_list:
                dev_name = evdev.InputDevice(dev).name
                if(name.lower() in dev_name.lower()):
                    found = True
                    self._dev_path = dev
                    break
            time.sleep(0.5)
        
        if(not found):
            raise IOError('No gamepad controller with name "' + name + '" found')
        else:
            self._dev = evdev.InputDevice(self._dev_path)
            # ToDo: Add safety check that the given controller really has these axes
            self._axes = abs_axes
            self._dpad = dpad
            self._btns = buttons
            self._is_connected = True
        

    def check_connection(self):
        '''
            Check whether the gamepad controller is available
        '''
        dev_list = evdev.list_devices()
        self._is_connected = False
        for dev in dev_list:
            try:
                dev_name = evdev.InputDevice(dev).name
            except FileNotFoundError:
                pass
            if(self._dev.name.lower() ==  dev_name.lower()):
                self._is_connected = True

        return self._is_connected 


    def read_axes(self, ax_list: List[str]):
        '''
            Read the given absolute axes from the gamepad and map the values to [-1, 1]
        '''
        if(not self._is_connected):
            raise IOError('No gamepad controller with name is connected')

        values = []
        for ax in ax_list:
            if(ax in list(self._axes.keys())):
                values.append((self._dev.absinfo(self._axes[ax]).value - (self._dev.absinfo(self._axes[ax]).max + 1)/2)/((self._dev.absinfo(self._axes[ax]).max + 1)/2))
            else:
                raise ValueError('Controller does not have axis ' + ax)
            
        return values


    def read_dpad(self):
        '''
            Read the dpad and return a dict
        '''
        if(not self._is_connected):
            raise IOError('No gamepad controller with name is connected')

        values = {'DP_up': 0, 'DP_down': 0, 'DP_right': 0, 'DP_left': 0}
        for ax in list(self._dpad.keys()):
            if('X' in ax):
                val = self._dev.absinfo(self._dpad[ax]).value
                if(val == 1):
                    values['DP_right'] = 1
                elif(val == -1):
                    values['DP_left'] = 1
            else:
                val = self._dev.absinfo(self._dpad[ax]).value
                if(val == 1):
                    values['DP_down'] = 1
                elif(val == -1):
                    values['DP_up'] = 1
            
        return values


    def read_buttons(self, bt_list: List[int]):
        '''
            Read the given buttons and return their state as a list of booleans
        '''
        if(not self._is_connected):
            raise IOError('No gamepad controller with name is connected')

        values = []
        active = self._dev.active_keys()
        for bt in bt_list:
            if(bt in list(self._btns.keys())):
                values.append(self._btns[bt] in active)
            else:
                raise ValueError('Controller does not have button ' + bt)
        
        return values

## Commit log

2024-01-12 Make slight improvement to the schematics
2024-01-15 Add wiring schematic and baseplate dimensions
